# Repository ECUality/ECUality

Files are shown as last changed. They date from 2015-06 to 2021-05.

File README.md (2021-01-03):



# ECUality

This project is about taking full control of a dated fuel-injection system, and making that process easier to repeat. Currently, the system is built to run the engine in a 1984 VW vanagon. I aim to create a platform that bears adaptation requiring a minimum of external tools. 

ECUality differs from other ECU projects in that I avoid relying on complex tuning software, favoring simple map-tuning algorithms that run whenever the engine and O2 sensor are warm. 

More info [here](https://hackaday.io/project/4622-ecuality1).

## Install

1. Install the [Arduino IDE](https://www.arduino.cc/en/Main/Donate).
2. Clone the repository.
3. Connect an Arduino Mega 2560 to your computer's USB port.
4. Start the Arduino IDE.
5. Open `ECUality.ino` in the IDE.
6. Click "Upload". This will build the project, and upload the compiled firmware to your Arduino.

## License
[GNU GPLv3](LICENSE.txt)

## Dependencies
Platform: 8-bit Arduino Mega 2560 (The chip is AtMega 2560), atop the ECU shield specified in the shcematic and layout files.  
Build: Arduino IDE (uses gcc toolchain)

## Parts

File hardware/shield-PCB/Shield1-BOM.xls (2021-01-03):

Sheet: Part Locations
Item | location | nF | V | Package
2 | C1 | 10u | 35V | 1206
2 | C2 | 10u | 35V | 1206
2 | C3 | 10u | 35V | 1206
1 | C4 | 22u | 25V | 1206
8 | C5 | 100p | 50V | 1206 | First, select "Location" cell in item list
3 | C6 | 1u | 50V | 1206
2 | C7 | 10u | 35V | 1206
2 | C8 | 10u | 35V | 1206
4 | C9 | 220n | 50V | 1206
4 | C10 | 220n | 50V | 1206
4 | C11 | 220n | 50V | 1206
2 | C12 | 10u | 35V | 1206
6 | C13 | 4.7n | 50V | 1206
6 | C14 | 4.7n | 50V | 1206
5 | C15 | 100n | 50V | 1206
9 | C16 | 20p | 50V | 1206
4 | C17 | 220n | 50V | 1206
4 | C18 | 220n | 50V | 1206
7 | C19 | 1n | 50V | 1206
9 | C20 | 20p | 50V | 1206
2 | C21 | 10u | 35V | 1206
2 | C22 | 10u | 35V | 1206
8 | C23 | 100p | 50V | 1206
14 | R1 | 10k | 0.25W | 1206
15 | R2 | 4.7k | 0.25W | 1206
14 | R3 | 10k | 0.25W | 1206
18 | R4 | 10k | 0.25W | Trimmer
12 | R5 | 47k | 0.25W | 1206
19 | R6 | 0.04 | 5W | 27mm ax
16 | R7 | 18k | 600V | 1210
16 | R8 | 18k | 600V | 1210
16 | R9 | 18k | 600V | 1210
16 | R10 | 18k | 600V | 1210
16 | R11 | 18k | 600V | 1210
16 | R12 | 18k | 600V | 1210
16 | R13 | 18k | 600V | 1210
16 | R14 | 18k | 600V | 1210
15 | R15 | 4.7k | 0.25W | 1206
15 | R16 | 4.7k | 0.25W | 1206
13 | R17 | 22k | 0.25W | 1206
13 | R18 | 22k | 0.25W | 1206
15 | R19 | 4.7k | 0.25W | 1206
13 | R20 | 22k | 0.25W | 1206
11 | R21 | 220k | 0.25W | 1206
11 | R22 | 220k | 0.25W | 1206
11 | R23 | 220k | 0.25W | 1206
11 | R24 | 220k | 0.25W | 1206
10 | R25 | 1M | 0.25W | 1206
13 | R27 | 22k | 0.25W | 1206
13 | R28 | 22k | 0.25W | 1206
17 | R29 | 4.02k | 0.25W | 1206
17 | R30 | 4.02k | 0.25W | 1206
17 | R31 | 4.02k | 0.25W | 1206
17 | R32 | 4.02k | 0.25W | 1206
20 | D1 | Zener | 20V | SOD123
21 | D2 | Zener | 4.7V | SOD123
 | D7 | Zener | 4.7V | SOD123
22 | IC1 | buffer |  | SOT23-5
22 | IC2 | buffer |  | SOT23-5
22 | IC3 | buffer |  | SOT23-5
23 | IC4 | Vreg | 3.3V | SOT223
22 | IC5 | buffer |  | SOT23-5
29 | IC6 | Ign./Inj. IC |  | SO32W
43 | IC7 | comparator | 5V | SOT23-5
24 | IC8 | Vreg | 5V 1% | SOT223
24 | IC9 | Vreg | 5V 1% | SOT223
35 | IC11 | knock_IC |  | SO20L
26 | Q1 | IGBT | 390V | D2PAK
26 | Q2 | IGBT | 390V | D2PAK
26 | Q3 | IGBT | 390V | D2PAK
26 | Q4 | IGBT | 390V | D2PAK
27 | Q5 | P-MOS | 40V | D-PAK
28 | U$1 | Conn. | VW | 25-pin
30 | U$3 | SD holder
31 | U$4 | WBO2 controller
32 | Q6 | N-MOS | 3.3A | SOT23-3
33 | Q7 | N-MOS | 300mA | SOT23-3
34 | Q8 | Hi-side |  | D-PAK5
36 | QF1 | Crystal | 16MHz | HC49U
37 | ARD | Mega2560
38 | XB1 | X-bee 1
39 | FUSE1 | PTC fuse | .1A | 1206
40 | H1 | pin-header | 1x8 | .1"
40 | H2 | pin-header | 1x8 | .1"
40 | H3 | pin-header | 1x8 | .1"
40 | H4 | pin-header | 1x8 | .1"
41 | H5 | pin-header | 2x8 | .1"
42 | H6 | fem-header | 1x10 | 2mm
42 | H7 | fem-header | 1x10 | 2mm
44 | H8 | fem-header | 2x5 | .1"
45 | H9 | pin-header | 2x5 | .1"

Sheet: Unique Items
Item | location | nF | V | Package | Qty | pkg. type | Dist. PN
1 | C4 | 22u | 25V | 1206 | 1 | smt | 1276-3299-1-ND
2 | C1 C2 C3 C7 C8 C12 C21 C22 | 10u | 35V | 1206 | 8 | smt | 1276-3100-1-ND
3 | C6 | 1u | 50V | 1206 | 1 | smt | 1276-1068-1-ND
4 | C9 C10 C11 C17 C18 | 220n | 50V | 1206 | 5 | smt | 1276-1106-1-ND
5 | C15 | 100n | 50V | 1206 | 1 | smt | 1276-1017-1-ND
6 | C13 C14 | 4.7n | 50V | 1206 | 2 | smt | 1276-1309-1-ND
7 | C19 | 1n | 50V | 1206 | 1 | smt | 1276-1050-1-ND
8 | C5 C23 | 100p | 50V | 1206 | 2 | smt | 1276-1053-1-ND
9 | C16 C20 | 20p | 50V | 1206 | 2 | smt | 1276-2819-1-ND
10 | R25 | 1M | 0.25W | 1206 | 1 | smt | 311-1.00MFRCT-ND
11 | R21 R22 R23 R24 | 220k | 0.25W | 1206 | 4 | smt | 311-220KFRCT-ND
12 | R5 | 47k | 0.25W | 1206 | 1 | smt | 311-47.0KFRCT-ND
13 | R17 R18 R20 R27 R28 | 22k | 0.25W | 1206 | 5 | smt | 311-22KERCT-ND
14 | R1 R3 | 10k | 0.25W | 1206 | 2 | smt | 311-10.0KFRCT-ND
15 | R2 R15 R16 R19 | 4.7k | 0.25W | 1206 | 4 | smt | 311-4.70KFRCT-ND
16 | R7 R8 R9 R10 R11 R12 R13 R14 | 18k | 600V | 1210 | 8 | smt | RHM18KAICT-ND
17 | R29 R30 R31 R32 | 4.02k | 0.25W | 1206 | 4 | smt | RHM4.02KAICT-ND | 29
18 | R4 | 10k | 0.25W | Trimmer | 1 | smt | ST4ETA103CT-ND
19 | R6 | 0.04 | 5W | 27mm ax | 1 | thru-hole | 15FR040E-ND
20 | D1 | Zener | 20V | SOD123 | 1 | smt | 568-6359-1-ND
21 | D2 | Zener | 4.7V | SOD123 | 1 | smt | 568-6369-1-ND
22 | IC1 IC2 IC3 IC5 | buffer |  | SOT23-5 | 4 | smt | 296-11603-1-ND
23 | IC4 | Vreg | 3.3V | SOT223 | 1 | smt | AP1117IE33G-13DICT-ND
24 | IC8 IC9 | Vreg | 5V 1% | SOT223 | 2 | smt | AP1117E50GDICT-ND |  | MC33269ST-3.3T3GOSCT-ND
25 |  | op-amp | 5V | SOT23-5 | 0 | smt | MCP601T-E/OTCT-ND
26 | Q1 Q2 Q3 Q4 | IGBT | 390V | D2PAK | 4 | smt | ISL9V5036S3STCT-ND
27 | Q5 | P-MOS | 40V | D-PAK | 1 | smt | SUD50P04-09L-E3CT-ND
28 | U$1 | Conn. | VW | 25-pin | 1 | thru-hole | Re-used from VW original
29 | IC6 | Ign./Inj. IC |  | SO32W | 1 | smt | MCZ33810EK-ND
30 | U$3 | SD holder |  |  | 1 | thru-hole | HR1941CT-ND |  | top right pad needs to move right, two bottom pads need to have solder-stop masked (they
31 | U$4 | WBO2 controller |  |  | 1 | smt | Empty |  | re covered
32 | Q6 | N-MOS | 3.3A | SOT23-3 | 1 | smt | SI2304DDS-T1-GE3CT-ND
33 | Q7 | N-MOS | 300mA | SOT23-3 | 1 | smt | 568-1369-1-ND
34 | Q8 | Hi-side |  | D-PAK5 | 1 | smt | BTS6133DCT-ND
35 | IC11 | knock_IC |  | SO20L | 1 | thru-hole | 296-34575-5-ND
36 | QF1 | Crystal | 16MHz | HC49U | 1 | NA | XC1925-ND
37 | ARD | Mega2560 |  |  | 1 | thru-hole | 1050-1018-ND
38 | XB1 | X-bee 1 |  |  | 1 | smt | XB24-AWI-001-ND
39 | FUSE1 | PTC fuse | .1A | 1206 | 1 | smt | 507-1477-1-ND
40 | H1 H2 H3 H4 | pin-header | 1x8 | .1" | 4 | smt | 732-5371-ND
41 | H5 | pin-header | 2x8 | .1" | 1 | smt | 732-5466-5-ND
42 | H6 H7 | fem-header | 1x10 | 2mm | 2 | thru-hole | S5751-10-ND
43 | IC7 | comparator | 5V | SOT23-5 | 1 | smt | MCP6561UT-E/OTCT-ND
44 | H8 | fem-header | 2x5 | .1" | 1 | smt | S5714-ND
45 | H9 | pin-header | 2x5 | .1" | 1 | thru-hole | 609-3372-ND
 | notes:

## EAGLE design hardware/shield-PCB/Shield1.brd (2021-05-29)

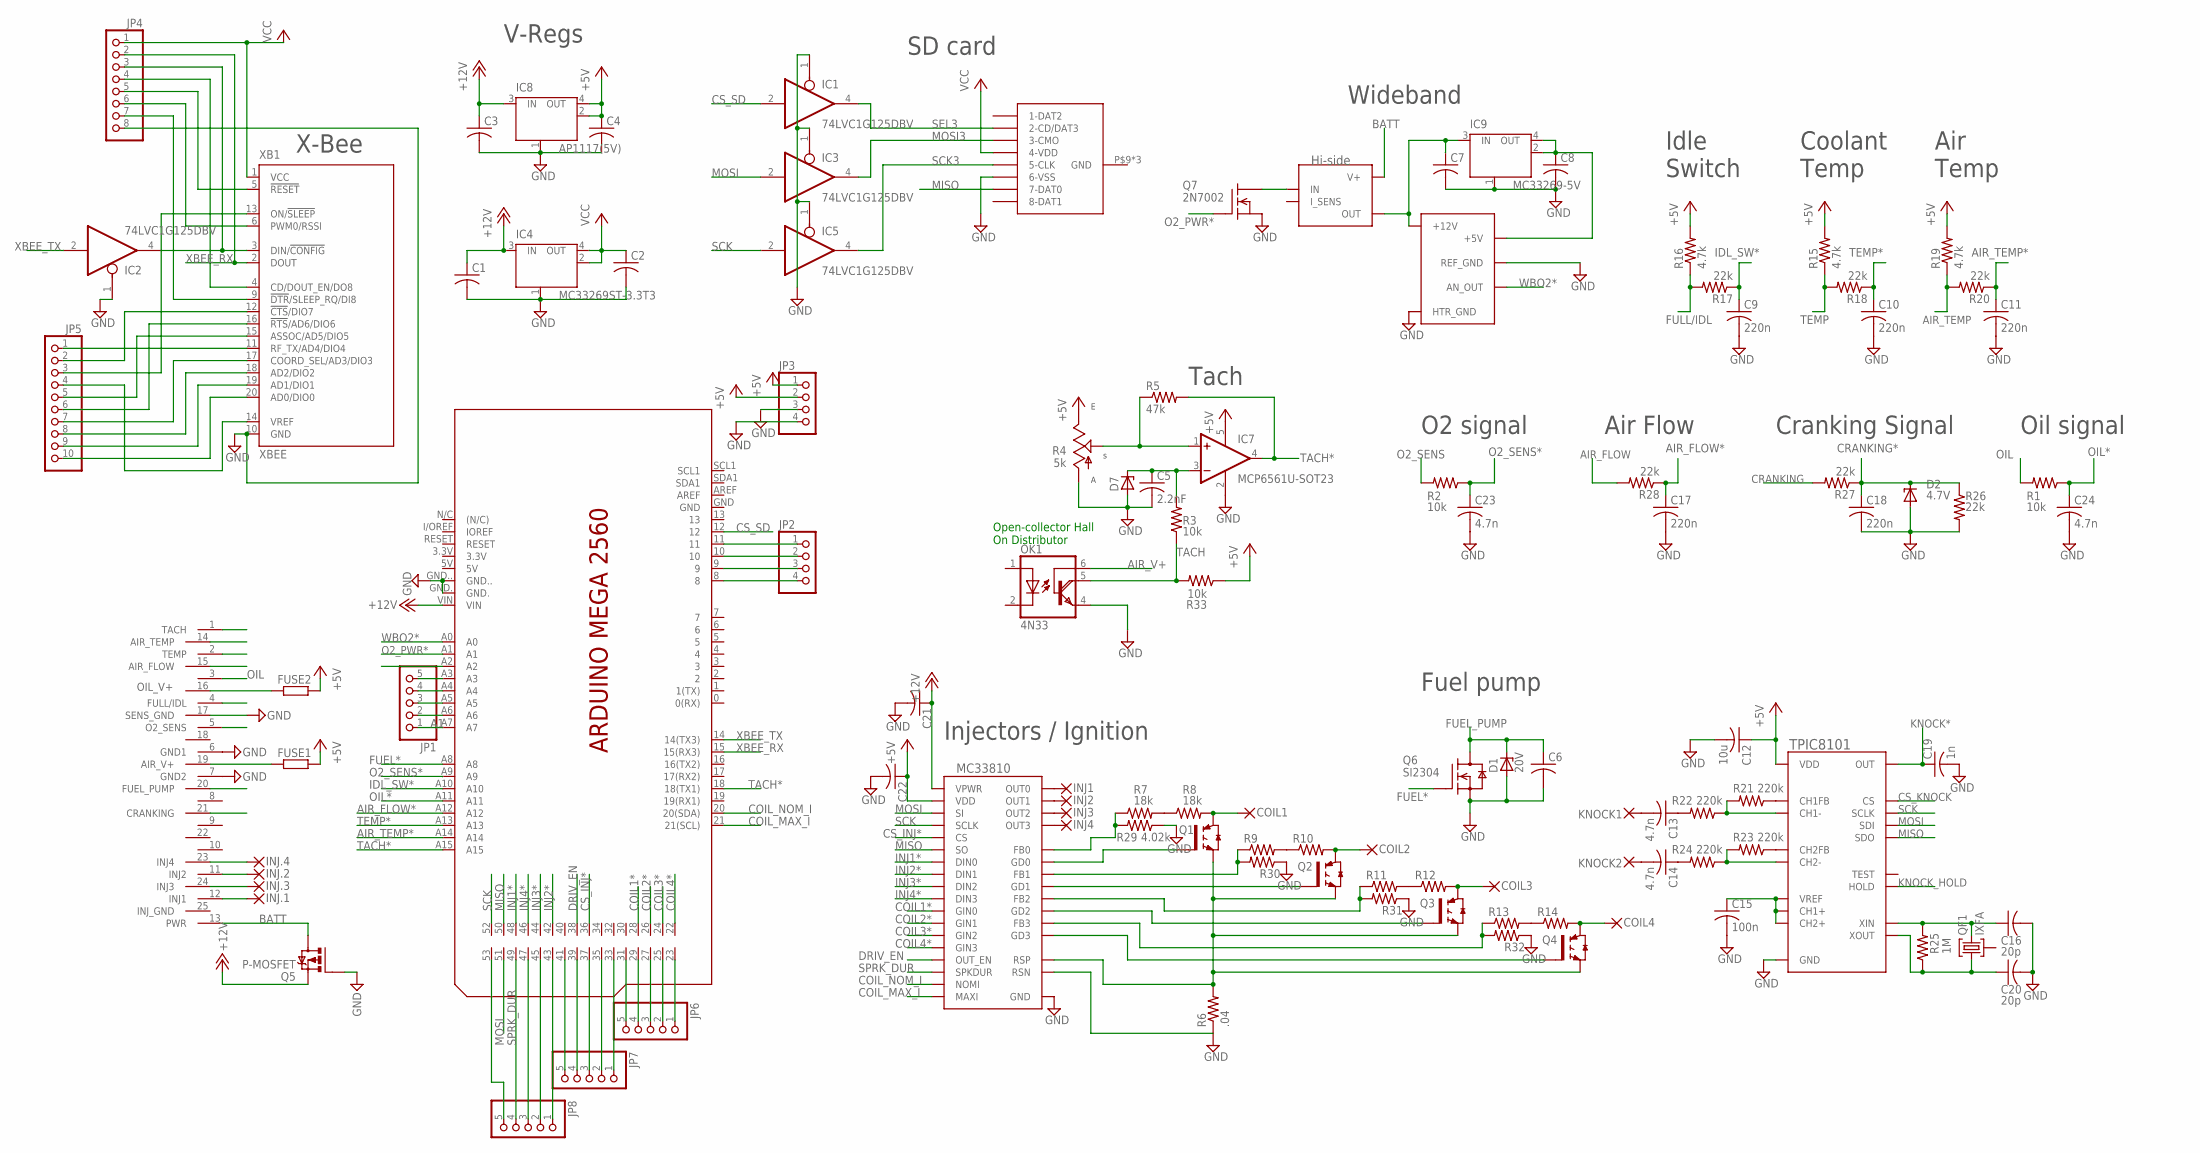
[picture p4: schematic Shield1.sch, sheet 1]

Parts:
C1, C2, C3, C4, C6, C7, C8, C21, C22: C-USC1206; C1206
C5: 2.2nF; C1206
C9, C10, C11, C17, C18: 220n; C1206
C12: 10u; C1206
C13, C14, C23, C24: 4.7n; C1206
C15: 100n; C1206
C16, C20: 20p; C1206
C19: 1n; C1206
COIL1, COIL2, COIL3, COIL4: 2,15/1,0
D1: 20V; SOD123
D2: 4.7V; SOD123
D7: ZENER-DIODESOD80C; SOD80C
FUSE1, FUSE2: R-EU_R1206W; R1206W
IC1, IC2, IC3, IC5: 74LVC1G125DBV; SOT23-5
IC4: MC33269ST-3.3T3; SOT223
IC6: MC33810SSOP; SSOP32_POWERPAD
IC7: MCP6561U-SOT23; SOT23-5
IC8: AP1117(5V); SOT223
IC9: MC33269-5V; SOT223
IC11: KNOCK_SENS_IC_TPIC8101; SO20L
INJ1, INJ2, INJ3, INJ4, INJ.1, INJ.2, INJ.3, INJ.4: 2,15/1,2
JP1, JP6, JP7, JP8: PINHD-1X5; 1X05
JP2, JP3: PINHD-1X4; 1X04
JP4: PINHD-1X8; 1X08
JP5: PINHD-1X10NARROW; 1X10-N
KNOCK1, KNOCK2: 2,15/1,0
OK1: 4N33; DIL06
Q1, Q2, Q3, Q4: ISL9V5036S3S; D2PACK
Q5: P-MOSFET; D-PAK_TO252AA
Q6: SI2304; SOT23
Q7: 2N7002; SOT23
Q8: BTS6133; DPACK_5
QF1: IXFA; HC49U
R1, R2, R3, R33: 10k; R1206
R4: 5k; 50/45J
R5: 47k; R1206
R6: .04; 0840/27
R7, R8: 18k; R1210W
R9, R10, R11, R12, R13, R14: R-US_R1210W; R1210W
R15, R16, R19: 4.7k; R1206
R17, R18, R20, R26, R27, R28: 22k; R1206
R21, R22, R23, R24: 220k; R1206
R25: 1M; R1206
R29: 4.02k; R1206
R30, R31, R32: R-US_R1206; R1206
U$1: VW_84_CONN
U$3: HI-ROSE-DM3D; DM3D-SF
U$4: ECOTRON_ALM-BOARD; ECOTRONS_ALM-BOARD
U$9: MEGA2560_SMD; MEGA_NO-PWR/USB/ICSP_SMD
XB1: XBEE

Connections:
+5V: C4.1, C12.1, C22.1, FUSE1.2, FUSE2.2, IC6.8 (VDD), IC7.5 (V+), IC8.2 (OUT), IC8.4 (OUT), IC11.1 (VDD), JP3.1, JP3.2, R4.1 (E), R15.2, R16.2, R19.2, R33.1
+12V: C1.1, C3.1, C21.1, IC4.3 (IN), IC6.25 (VPWR), IC8.3 (IN), Q5.3 (S), U$9.VIN
A1: JP1.1, U$9.A7
AIR_FLOW: R28.2, U$1.15 (AIR_FLOW)
AIR_FLOW*: C17.1, R28.1, U$9.A12
AIR_TEMP: R19.1, R20.2, U$1.14 (AIR_TEMP)
AIR_TEMP*: C11.1, R20.1, U$9.A14
AIR_V+: FUSE1.1, OK1.6 (B), U$1.19 (AIR_V+)
BATT: Q5.4 (D), Q8.3 (V+), U$1.13 (PWR)
COIL1: COIL1.1, Q1.2 (C), R8.2
COIL1*: IC6.24 (GIN0), U$9.28
COIL2: COIL2.1, Q2.2 (C), R10.2
COIL2*: IC6.23 (GIN1), U$9.26
COIL3: COIL3.1, Q3.2 (C), R12.2
COIL3*: IC6.22 (GIN2), U$9.24
COIL4: COIL4.1, Q4.2 (C), R14.2
COIL4*: IC6.21 (GIN3), U$9.22
COIL_MAX_I: IC6.29 (MAXI), U$9.21 (21(SCL))
COIL_NOM_I: IC6.28 (NOMI), U$9.20 (20(SDA))
CRANKING: R27.2, U$1.21 (CRANKING)
CRANKING*: C18.1, D2.C, R26.1, R27.1
CS_INJ*: IC6.4 (CS), U$9.36
CS_KNOCK: IC11.8 (CS)
CS_SD: IC1.2 (I), U$9.12
DRIV_EN: IC6.9 (OUT_EN), U$9.38
FUEL*: Q6.1 (G), U$9.A8
FUEL_PUMP: C6.1, D1.C, Q6.3 (D), U$1.20 (FUEL_PUMP)
FULL/IDL: R16.1, R17.2, U$1.4 (FULL/IDL)
GND: C1.2, C2.2, C3.2, C4.2, C5.2, C6.2, C7.2, C8.2, C9.2, C10.2, C11.2, C12.2, C15.2, C16.2, C17.2, C18.2, C19.2, C20.2, C21.2, C22.2, C23.2, C24.2, D1.A, D2.A, D7.A, IC1.1 (OE), IC1.3 (GND), IC2.1 (OE), IC2.3 (GND), IC3.1 (OE), IC3.3 (GND), IC4.1 (GND/ADJ), IC5.1 (OE), IC5.3 (GND), IC6.27 (RSN), IC6.GND, IC6.V1 (GND), IC6.V2 (GND), IC6.V3 (GND), IC6.V4 (GND), IC6.V5 (GND), IC7.2 (V-), IC8.1 (GND/ADJ), IC9.1 (GND/ADJ), IC11.2 (GND), JP3.3, JP3.4, JP4.8, OK1.4 (E), Q5.1 (G), Q6.2 (S), Q7.2 (S), R4.3 (A), R6.1, R26.2, R29.1, R30.1, R31.1, R32.1, U$1.6 (GND1), U$1.7 (GND2), U$1.17 (SENS_GND), U$3.P$3 (6-VSS), U$3.P$9 (GND), U$3.P$10 (GND), U$3.P$11 (GND), U$4.P$2 (HTR_GND), U$4.P$3 (REF_GND), U$4.P$6 (REF_GND), U$4.P$9 (HTR_GND), U$9.GND., U$9.GND.., XB1.10 (GND)
IDL_SW*: C9.1, R17.1, U$9.A10
INJ1: INJ.1.1, U$1.12 (INJ1)
INJ1*: IC6.10 (DIN0), U$9.48
INJ2: INJ.2.1, U$1.11 (INJ2)
INJ2*: IC6.11 (DIN1), U$9.42
INJ3: INJ.3.1, U$1.24 (INJ3)
INJ3*: IC6.12 (DIN2), U$9.44
INJ4: INJ.4.1, U$1.23 (INJ4)
INJ4*: IC6.13 (DIN3), U$9.46
KNOCK*: C19.1, IC11.4 (OUT), U$9.A2
KNOCK_HOLD: IC11.7 (HOLD)
MISO: IC6.7 (SO), IC11.11 (SDO), U$3.P$2 (7-DAT0), U$9.50
MOSI: IC3.2 (I), IC6.6 (SI), IC11.12 (SDI), U$9.51
MOSI3: IC3.4 (O), U$3.P$6 (3-CMO)
unnamed: C5.1, D7.C, IC7.3 (-IN), R3.2
unnamed: C7.1, IC9.3 (IN), Q8.1 (OUT), Q8.5 (OUT), U$4.P$1 (+12V), U$4.P$10 (+12V)
unnamed: IC6.26 (RSP), Q1.3 (E), Q2.3 (E), Q3.3 (E), Q4.3 (E), R6.2
unnamed: IC6.14 (GD1), Q2.1 (G)
unnamed: IC6.2 (FB0), R7.1, R29.2
unnamed: IC6.3 (GD0), Q1.1 (G)
unnamed: Q7.3 (D), Q8.2 (IN)
unnamed: IC6.1 (OUT0), INJ1.1
unnamed: IC11.19 (CH1-), R21.2, R22.1
unnamed: IC7.1 (+IN), R4.2 (S), R5.1
unnamed: IC6.15 (FB1), R9.1, R30.2
unnamed: IC6.30 (GD2), Q3.1 (G)
unnamed: IC2.4 (O), JP4.3, XB1.3 (DIN/!CONFIG)
unnamed: C8.1, IC9.2 (OUT), IC9.4 (OUT), U$4.P$4 (+5V)
unnamed: IC6.31 (FB2), R11.1, R31.2
unnamed: IC6.19 (GD3), Q4.1 (G)
unnamed: IC11.18 (CH1FB), R21.1
unnamed: IC6.18 (FB3), R13.1, R32.2
unnamed: C13.1, R22.2
unnamed: IC11.16 (CH2-), R23.2, R24.1
unnamed: C14.1, R24.2
unnamed: C15.1, IC11.3 (VREF), IC11.15 (CH2+), IC11.20 (CH1+)
unnamed: IC11.17 (CH2FB), R23.1
unnamed: IC6.16 (OUT1), INJ2.1
unnamed: IC6.32 (OUT2), INJ3.1
unnamed: C20.1, IC11.10 (XOUT), QF1.1, R25.1
unnamed: C16.1, IC11.9 (XIN), QF1.3, R25.2
unnamed: IC6.17 (OUT3), INJ4.1
unnamed: C13.2, KNOCK1.1
unnamed: C14.2, KNOCK2.1
unnamed: JP6.1, U$9.23
unnamed: R7.2, R8.1
unnamed: R9.2, R10.1
unnamed: R11.2, R12.1
unnamed: R13.2, R14.1
unnamed: JP1.2, U$9.A6
unnamed: JP1.3, U$9.A5
unnamed: JP1.4, U$9.A4
unnamed: JP1.5, U$9.A3
unnamed: JP2.1, U$9.11
unnamed: JP2.2, U$9.10
unnamed: JP2.3, U$9.9
unnamed: JP2.4, U$9.8
unnamed: JP4.4, XB1.4 (CD/DOUT_EN/DO8)
unnamed: JP4.5, XB1.5 (!RESET)
unnamed: JP4.6, XB1.6 (PWM0/RSSI)
unnamed: JP5.10, XB1.20 (AD0/DIO0)
unnamed: JP5.9, XB1.19 (AD1/DIO1)
unnamed: JP5.8, XB1.18 (AD2/DIO2)
unnamed: JP5.7, XB1.17 (COORD_SEL/AD3/DIO3)
unnamed: JP5.6, XB1.16 (!RTS!/AD6/DIO6)
unnamed: JP5.5, XB1.15 (ASSOC/AD5/DIO5)
unnamed: JP5.4, XB1.14 (VREF)
unnamed: JP5.3, XB1.13 (ON/!SLEEP)
unnamed: JP5.2, XB1.12 (!CTS!/DIO7)
unnamed: JP5.1, XB1.11 (RF_TX/AD4/DIO4)
unnamed: JP4.7, XB1.9 (!DTR!/SLEEP_RQ/DI8)
unnamed: JP6.2, U$9.25
unnamed: JP6.3, U$9.27
unnamed: JP6.4, U$9.29
unnamed: JP6.5, U$9.31
unnamed: JP7.1, U$9.33
unnamed: JP7.2, U$9.35
unnamed: JP7.3, U$9.37
unnamed: JP7.4, U$9.39
unnamed: JP7.5, U$9.41
unnamed: JP8.1, U$9.43
unnamed: JP8.2, U$9.45
unnamed: JP8.3, U$9.47
unnamed: JP8.5, U$9.53
O2_PWR*: Q7.1 (G), U$9.A1
O2_SENS: R2.2, U$1.5 (O2_SENS)
O2_SENS*: C23.1, R2.1, U$9.A9
OIL: R1.2, U$1.3
OIL*: C24.1, R1.1, U$9.A11
OIL_V+: FUSE2.1, U$1.16
SCK: IC5.2 (I), IC6.5 (SCLK), IC11.13 (SCLK), U$9.52
SCK3: IC5.4 (O), U$3.P$4 (5-CLK)
SEL3: IC1.4 (O), U$3.P$7 (2-CD/DAT3)
SPRK_DUR: IC6.20 (SPKDUR), JP8.4, U$9.49
TACH: OK1.5 (COL), R3.1, R33.2, U$1.1 (TACH)
TACH*: IC7.4 (OUT), R5.2, U$9.18 (18(TX1)), U$9.A15
TEMP: R15.1, R18.2, U$1.2 (TEMP)
TEMP*: C10.1, R18.1, U$9.A13
VCC: C2.1, IC1.5 (VCC), IC2.5 (VCC), IC3.5 (VCC), IC4.2 (OUT), IC4.4 (OUT), IC5.5 (VCC), JP4.1, U$3.P$5 (4-VDD), XB1.1 (VCC)
WBO2*: U$4.P$7 (AN_OUT), U$9.A0
XBEE_RX: JP4.2, U$9.15 (15(RX3)), XB1.2 (DOUT)
XBEE_TX: IC2.2 (I), U$9.14 (14(TX3))

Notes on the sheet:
Tach
Fuel pump
SD card
O2 signal
Injectors / Ignition
X-Bee
V-Regs
Wideband
Idle Switch
Air Temp
Coolant Temp
Air Flow
Cranking Signal
Oil signal
Open-collector Hall On Distributor

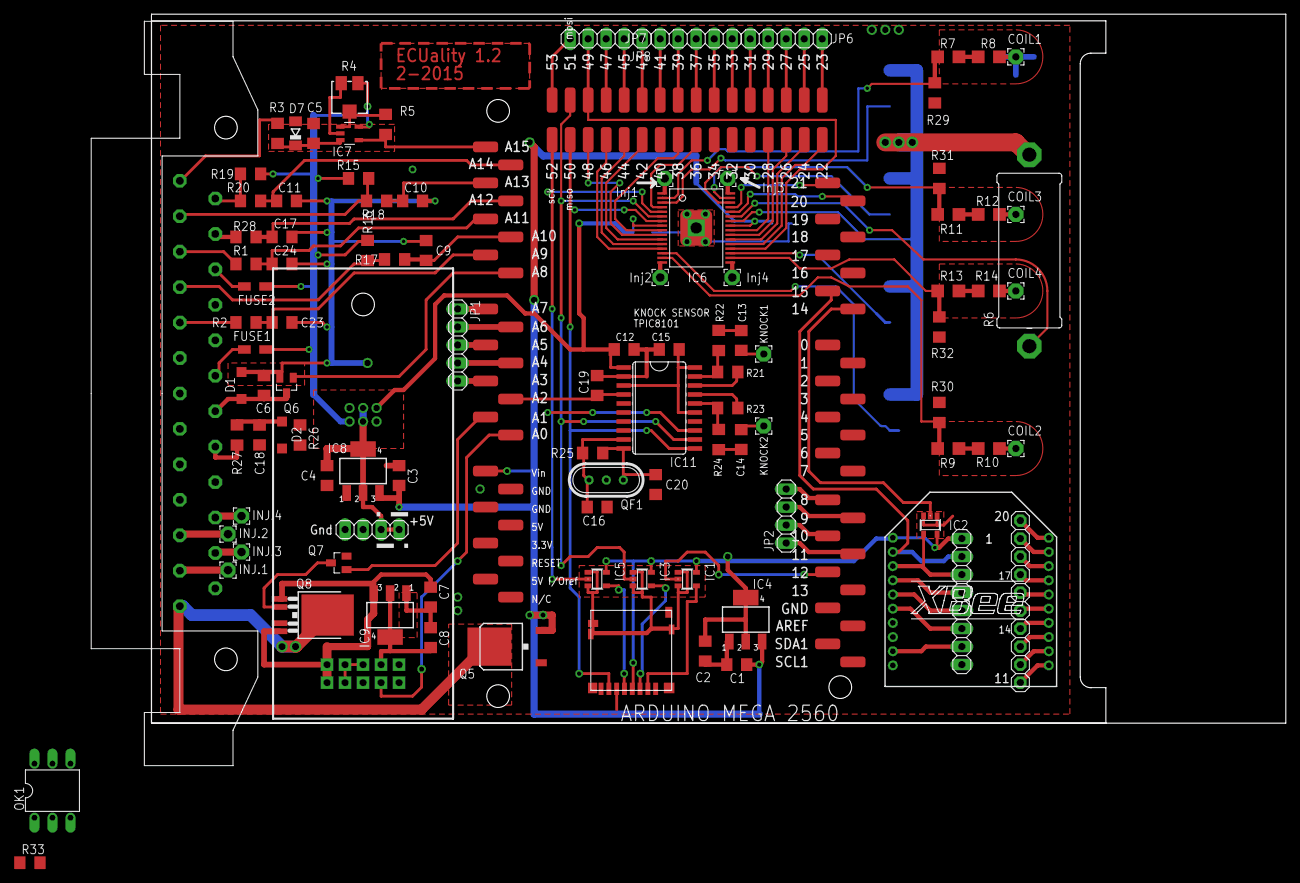
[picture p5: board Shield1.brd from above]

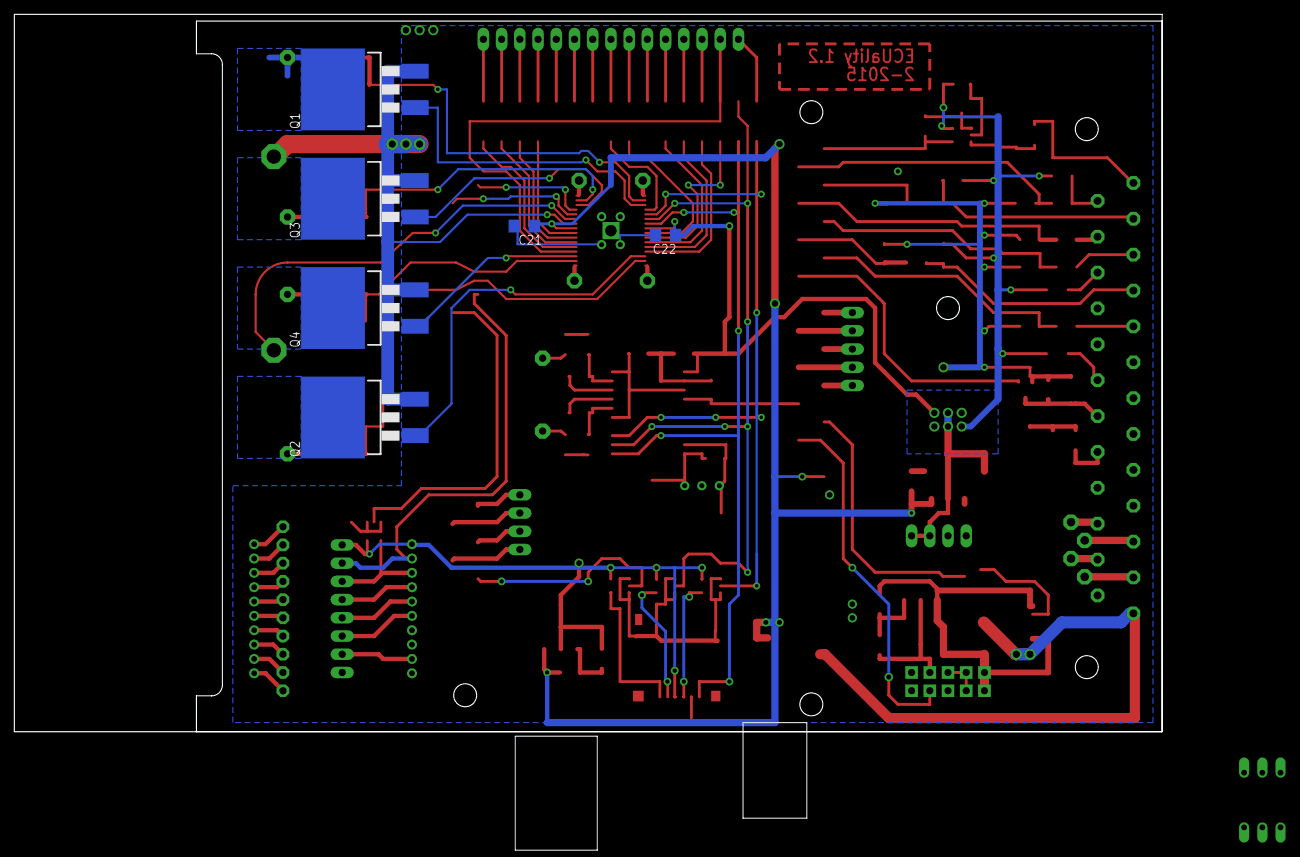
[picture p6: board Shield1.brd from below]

Board: 2 copper layers, 160.0 x 100.0 mm, 109 parts (7 on the bottom side), 129 nets.

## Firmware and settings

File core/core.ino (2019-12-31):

#include "Defines.h"
#include "Globals.h"
#include "Arrays.h"
#include "Map.h"
#include "Scale.h"
#include "Parameter.h"
#include "ECUSerial.h"
#include "ECUProtocol.h"
#include "Interpolation.h"
#include "EEIndex.h"
#include "EEPROMAnything.h"
#include "ECUPins.h"
#include "FuelTweaker.h"
#include "MovingAverage.h"
#include "SPICommands.h"
#include <EEPROM.h>
#include <SPI.h>

// Data: 60e6 us/min   16us/timer tic (256 prescale, 16Mhz)   
// quarter-rev of dizzy is measured 1/2 rev of crank
// us/min / us/tic  = tics/min
// tics / min * rev/sample = rev/min * tics/sample
// rev/min * tics/sample / tics/sample = rev/min 
// 60e6 / 16 / 2 = 1,875,000 rpm * tics/sample
// so rpm = 1875000/(spark_period)

#define TICS_PER_TACH 1875000

void addTask(void(*task)(), unsigned int ms);	// for some reason, this needs a prototype before it is used where others don't. 

void setup()
{
	char enable = 0;
	simulate_tach_en = 0;					// default to debug resources off. 
	fuel_pump_en = injector_en = coil_en = 1;	// default to having driving resources on. 

	ESerial.begin(9600);
	//Serial.begin(115200);

	InitSPI();

	NameParams();

	// There are 3 levels of priority in this program.  
	// Every event falls into one of these categories
	// 1: Injector duration timing (highest)
	// 2: Tasks that happen periodically (middle)
	// 3: Responses to the user (lowest)
	//
	// The following "task" array contains the periods of the level-2 events. 
	// Execution of these events can be interrupted by a level-1 event. 
	// These events will interrupt execution of a level-3 event. 
	n_tasks = 0;
	addTask(simulatedTachEdge, 20);
	addTask(readAirFlow, 50);
	addTask(readO2Sensor, 50);
	addTask(calcRPMandDwell, 50);
	addTask(calcInjDuration, 50);
	addTask(calcIgnitionMarks, 50);
	addTask(readAirTemp, 250);
	addTask(readCoolantTemp, 250);
	addTask(readOilPressure, 250);
	addTask(autoReport, 1000);
	addTask(updateRunCondition, 100);
	addTask(tweakFuel, TWEAK_FREQ_MS);

	i_autoreport = 8;		// this is referenced to delay next autoreport message.  

	// input interrupt pin
	digitalWrite(cs_knock_pin, HIGH);
	digitalWrite(cs_inj_pin, HIGH);
	digitalWrite(cs_sd_pin, HIGH);

	setPinModes(inputs, INPUT);
	setPinModes(outputs, OUTPUT);
	pinMode(40, INPUT);		// the other hooked-up inj1_pin. 
	pinMode(index_pin, INPUT_PULLUP);	// enable pullup on index pin. 

	digitalWrite(cs_inj_pin, HIGH);
	digitalWrite(cs_knock_pin, HIGH);
	digitalWrite(cs_sd_pin, HIGH);


	inj_duration = 5;
	tach_period = 0;

	Map::clear(&change_map);
	good_ee_loads = loadData(NULL);		// load data from EE.

	initProtocol();						// set up protocol. 

	// TIMERS
	// Configure Timer1 for task scheduling.  Hits ICR1 every 2ms and runs interrupt. 
	TCCR1A = 0;				// disables all output compare modules and clears WGM1<0-1> 
	TCCR1B = _BV(CS10);		// sets prescaler to 1:1, and turns on timer, clears WGM1<3:2>
	TCCR1B |= _BV(WGM12) | _BV(WGM13);	// 
	// WGM1<3:0> = 1,1,0,0 = mode 12 "CTC" with top = ICR.   positive slope only, 
	ICR1 = 32000;			// 16 tics / us * 2000us = 32000tics in 2ms.
	TIMSK1 = _BV(ICIE1);

	// Configure Timer3 for measuring injector pulse duration (using interrupt)
	TCCR3A = 0;							// clear control register A 
	TCCR3B = _BV(CS31) | _BV(CS30);		// start the timer at clk/64 prescale. 

	TIMSK3 |= _BV(OCIE3A);				// enable output compare A interrupt on timer 3
	//TIMSK3 |= _BV(TOIE3);				// enable timer overflow interrupt on timer 3 (just-in-case-of-something-weird)

	// Configure Timers 4 and 5 for measuring ignition dwell (using interrupt)
	TCCR4A = TCCR5A = 0;				// clear control register A 
	TCCR4B = _BV(CS42);					// start the timers at clk/256 prescale. = 16us per tic. 
	TCCR5B = _BV(CS52);
	//TCCR4B = _BV(CS42) | _BV(CS40);		// start the timer at clk/1024 prescale. = 64us per tic. 

	// enable timer overflow interrupt for non-running and slow-cranking issues
	TIMSK4 |= _BV(TOIE4);	// this affects rpm calculation for low RPM
	TIMSK5 |= _BV(TOIE5);


	// Timer4 NOTE: updateDwell() enables or disables the ignition system by 
	// setting or clearing OCIE4A, the output compare interrupt enable bit. 
	// The Output compare interrupt is what starts the dwells.
	// It is important for engine-start that we NOT set OCIE4A here. 


	// disable the timer 0 interrupt.  This breaks millis() but prevents interference with pulse timing.
	// note: ECUSerial.cpp uses millis() to time communication-stream events.  
	//TIMSK0 &= 0x00;		

	// Configure Timer0 for generating a fast PWM.  16us period, 62.5kHz
	// CONFIG BITS:
	// WGM0<3:0>	= 0 (0000)	normal mode, counts up to 0xFFFF.  
	// COM0A<1:0>	= 2 (10)	clears OC0A on compare match so OCR0A represents "high" time. 
	// COM0B<1:0>	= 2 (10)	same as A.
	// CS0<2:0>		= 1 (001)	1:1 pre-scaling, timer running. 

	// next line: the input circuit inverts the signal, so a rising edge from the distributor produces a falling
	// edge at the Arduino.  We trigger when the tab enters the Hall sensor.  The hall sensor produces a high signal
	// when it is looking at a tab, so we want to trigger here on a FALLING edge. 

	attachInterrupt(tach_interrupt, isrTachEdge, FALLING);	// interrupt 4 maps to pin 19. 	
	attachInterrupt(coil_current_interrupt, isrCoilNominalCurrent, RISING);	// interrupt 3 maps to pin 20. 

	EEPROM_readAnything(ENABLE_ADDY, enable);
	if (enable)
		enableDrive();
	else
		ESerial.println(F("engine disabled"));		// said to either my forgetful self, or a van-thief. 

	EEPROM_readAnything(TWEAK_LOCK_ADDY, boss.lockout);
	if (boss.lockout)
		ESerial.println(F("tweaks locked"));		// lock bit set, no tuning. 

	auto_stat = 1; // turn on auto-reporting. 

	// following sets an 8ms timeout on dwell with soft shutdown. 
	// it must come some significant time after SPIInit().  Hence this placement. 
	SPIInitSparkMode();	
	_delay_us(1000);
	SPISetNOMI(nom_coil_current.value);
}

void addTask(void(*task)(), unsigned int ms)
{
	task_list[n_tasks] = task;
	ms_freq_of_task[n_tasks] = ms;
	n_tasks++;
}

void setPinModes(const uint8_t pins[], const uint8_t direction)
{
	char i = 0;
	while (1)
	{
		if (pins[i] == '\0')
			return;
		pinMode(pins[i], direction);
		++i;
	}
}

void loop()
{
	// reportStatus is queued for action in the task scheduler but called here because serial output
	// takes forever and doesn't have as high a priority as running the engine. 
	if (auto_stat == 2)
	{
		auto_stat = 1;
		reportStatus(status_mode);
	}

	// check for any available serial input, then parse and run the commands. 
	ESerial.executeCommand();	
}

void autoReport()
{
	if (auto_stat == 1)
		auto_stat = 2;
	return;
}

// Sensor reading functions
void readAirFlow()
{

	air_flow_d = -air_flow;
	air_flow = analogRead(air_flow_pin) >> 2;	// takes 100us.  Should shorten
	air_flow_d += air_flow;

	if (air_flow_d > 20)
	{
		n_air_faults++;
		//ESerial.print(F("!air flt: "));
		//ESerial.println(n_air_faults);
	}

	/*
	air_flow_snap += air_flow_d;

	if (air_flow_snap)
	{
		if (air_flow_snap > accel_stabilize_rate.value)
			air_flow_snap -= accel_stabilize_rate.value;
		else
			air_flow_snap = 0;
	} */
	

}
void readO2Sensor()
{
	//o2_d = -o2;
	o2 = analogRead(o2_pin);		// this takes 100us.  Should shorten
	o2 *= 5; 
	//o2_d += o2;
}
void readAirTemp() 
{
	air_temp = analogRead(air_temp_pin);
	air_temp = temp_scale.interpolate(air_temp);
}
void readCoolantTemp() 
{
	coolant_temp = analogRead(coolant_temp_pin);
	coolant_temp = temp_scale.interpolate(coolant_temp);
}
void readOilPressure()
{
	// .5V = 0psi  4.5V = 100psi.  25psi/V 
	// 25psi/V * 5V/1023tic = .1222 psi/tic
	// 1 psi ~ 8 tics. 
	oil_pressure = analogRead(oil_pressure_pin);
}
void calcRPMandDwell()
{
	static uint16_t old_rpm = 0;
	static uint16_t l_tach_period; // a local to this function copy of the volatile tach-period
	char cSREG;

	cSREG = SREG; // store SREG value - we don't assume GIE is set, we just copy it. 
	cli(); //disable interrupts during copy
	l_tach_period = tach_period;
	SREG = cSREG; /* restore SREG value (GIE-bit) to what it was*/

	// (60e6 us/min) / (4 us/tic)				= 15e6 tics/min
	// (tics/min) / (tach_period tics/pulse)	= pulses/min
	// pulses/min * (1 rev/pulse)				= 15e6 / tach_period 
	// we're pulsing the injectors (and measuring) every other tach input pulse, so it's 1:1 with crankshaft. 
	old_rpm = rpm;

	rpm = TICS_PER_TACH / l_tach_period;		// tach_period_copy doesn't get touched by interrupts, so this is safe. 
	rpm_d = old_rpm - rpm;
	avg_rpm.addSample(rpm);
	
	// This section says if we're running, and the rpm makes an abrupt change, 
	// it's a fault.  Log it.  
	if (!(run_condition & _BV(NOT_RUNNING) ) && (abs(rpm_d) > 1000))
	{
		if (rpm > avg_rpm.average)
		{
			n_rpm_hi_faults++;
			//ESerial.print("!RPM xtra ");
			//ESerial.println(n_rpm_hi_faults);
		}
		else
		{
			n_rpm_lo_faults++;
			//ESerial.print(F("!RPM miss "));
			//ESerial.println(n_rpm_lo_faults);
		}
	}
	
	// Only start charging coil if RPM is above a minimum and the rpm is relatively stable
	if ((rpm > MIN_IGN_RPM) && (abs(rpm_d) < (rpm >> 2)))
	{
		// clear the output compare flag. 
		TIFR4 &= ~(_BV(OCF4A) | _BV(OCF4B));	// clear the output compare flags. 
		TIFR5 &= ~(_BV(OCF5A) | _BV(OCF5B));	

		TIMSK4 |= (_BV(OCIE4A) | _BV(OCIE4B));	// enable the out.comp. interrupt (ignition system)
		TIMSK5 |= (_BV(OCIE5A) | _BV(OCIE5B));	

		digitalWrite(drv_en_pin, LOW);		// enable the driver chip (active low)
	}
	else
	{
		// disable ignition system. 
		TIMSK4 &= ~_BV(OCIE4A);			// this prevents the coil pin from being set
		TIMSK5 &= ~_BV(OCIE5A);	

		digitalWrite(drv_en_pin, HIGH);	// this starts a soft-shutdown - this pin active low
		PORTA &= 0xAA;			//  &= 1010_1010 turns off bits 0, 2, 4, and 6 (turns off all coils). 
	}

	// Use a fixed dwell for cranking.  Otherwise adjust the dwell to match a target current. 
	if (rpm < 800 && digitalRead(cranking_pin) ) {
		g_dwell = starting_dwell.value;		// High dwell during cranking
	}
	else {
		if (coil_current_flag) g_dwell--;
		else g_dwell++;
	}

}

// Pulse duration business
void calcInjDuration()
{
	static unsigned int l_inj_duration;
	static int accel_offset, choke_offset, air_temp_offset, global_offset;

	if (digitalRead(cranking_pin))
	{
		map_inj_duration = cranking_dur.value;
		choke_offset = adjustForColdEngine(cranking_dur.value, coolant_temp);	
		l_inj_duration = map_inj_duration + choke_offset;
	}

	else if (run_condition & _BV(IDLING))	// only consider cold engine enrichment for idle.  No global correction. 
	{
		map_inj_duration = idle_offset.value + idle_scale.interpolate(rpm);
		choke_offset = adjustForColdEngine(map_inj_duration, coolant_temp);
		l_inj_duration = map_inj_duration + choke_offset;
	}

	else if (run_condition & _BV(COASTING))
	{
		map_inj_duration = 0;
		l_inj_duration = 0;
	}

	else
	{
		// find nominal
		map_inj_duration = inj_map.interpolate(rpm, air_flow, &offset_map);

		// adjust for stuff
		accel_offset = adjustForAccel(air_flow);		// these should not be order dependent.  
		choke_offset = adjustForColdEngine(map_inj_duration, coolant_temp);
		air_temp_offset = adjustForAirTemp(map_inj_duration, air_temp);
		global_offset = (map_inj_duration >> 8)*global_correction.value;

		l_inj_duration = map_inj_duration + accel_offset + choke_offset + air_temp_offset + global_offset;
	}

	// output that shit
	char cSREG;
	cSREG = SREG; // store SREG value - we don't assume GIE is set, we just copy it. 
	cli(); //disable interrupts during copy
	inj_duration = l_inj_duration;
	SREG = cSREG; /* restore SREG value (GIE-bit) to what it was*/
}

// Ignition advance business - executes immediately after calcInjDuration()
void calcIgnitionMarks() {
	static uint16_t dwell_mark, spark_mark;	// these are the timer settings for the dwell start and spark events.  
	static uint16_t l_tach_period;			// this is a local copy of the volatile tach_period.
	char cSREG;

	const uint16_t edge_to_post = 256;
	static uint16_t spark_position;

	// here we calculate the centrifugal advance (rpm based) 
	// the units are 1/512ths of a revolution to facilitate division speeds. 
	// the original timing  
	advance = rpm_advance.interpolate(rpm);
	/*if (rpm < 1100) advance = 0;
	else if (rpm < 2124) advance = (((rpm - 1100) * 5) >> 8);
	else if (rpm < 2380) advance = 20 + (((rpm - 2124) * 3) >> 7);
	else if (rpm < 4428) advance = 26 + (((rpm - 2380) * 5) >> 10);
	else advance = 35;*/

	// now we do the vacuum advance.  (light-load advance)
	// The engine load is indicated by the injector duration (how much fuel enters the cylinder every cycle) 
	// At sea-level, the maximum injector duration is about 1,800.  The minimum while coasting is about 500.  
	// Assuming 1800 = 1bar (absolute) and a linear scale, then 500 = .278 bar(abs) = .722 bar vacuum (21inHg)
	// The manual calls for vacuum advance to begin at .21 bar and max out at .36 bar, 14 degrees (= 20/512'ths)
	// Using the injector duration scale, .21 bar vacuum = .79 bar absolute = .79*1800 = 1422 inj.
	// Similarly, .36 bar vacuum = .64 bar absolute = 1152 injector.  
	advance += vacuum_advance.interpolate(map_inj_duration);

	/*if (map_inj_duration < 1200) advance += 20;
	else if (map_inj_duration < 1456) advance += (((1456 - map_inj_duration) * 5) >> 6);*/

	// That's it.  The advance can vary from 0 to 55.  1/512ths =  0 - 38.7 degrees. 
	// At 3500 rpm and inj_duration of 1200, we'll have 31(rpm) and 20(load) = 51/512 = 36 degrees. 


	//spark_position = edge_to_post + 28 - advance;	// advance varies from 0 to 55, so we center it with + 28. 
	spark_position = initial_retard.value - advance;

	cSREG = SREG; // store SREG value - we don't assume GIE is set, we just copy it. 
	cli(); //disable interrupts during copy to the volatile variables. 
	l_tach_period = tach_period; 
	SREG = cSREG; /* restore SREG value (GIE-bit) to what it was*/

	spark_mark = ( (unsigned long)spark_position * l_tach_period ) >> 8;	// mark = (bdeg of event) * (timer tics per 256 bdeg) / (256 bdeg). 

	dwell_mark = spark_mark > g_dwell ? spark_mark - g_dwell : 0;	// Make sure dwell_mark is never negative.  

	// disable interrupts while Output Compares are set. 
	cSREG = SREG; // store SREG value - we don't assume GIE is set, we just copy it. 
	cli(); //disable interrupts during copy to the volatile variables. 
	v_spark_mark = spark_mark;
	v_dwell_mark = dwell_mark;
	SREG = cSREG; /* restore SREG value (GIE-bit) to what it was*/

}
int adjustForAccel(int air_flow)
{
	return 0;
}
int adjustForColdEngine(unsigned int nominal_duration, int coolant_temp)
{
	// calculates a positive offset as a percentage of nominal injector duration. 
	// % increase depends linearly on coolant temperature.  
	// takes a threshold temp and a rate (mx +b) for linear dependence on  coolant temperature
	unsigned long adjustment;
	
	if (run_condition & _BV(WARM))		// is engine already warm? 
		return 0;

	adjustment = choke_scale.interpolate(coolant_temp);
	adjustment *= nominal_duration;
	adjustment >>= 10;		// divide by 1024
	return int(adjustment);	// adjustment;		XXX
}
int adjustForAirTemp(int nominal_duration, int air_temp)
{
	return 0;
}

void tweakFuel()
{
	boss.tweak();
}
void updateRunCondition()
{
	char idl_or_full = !digitalRead(idl_full_pin);
	run_condition = 0;

	if (digitalRead(cranking_pin))
		run_condition |= _BV(CRANKING);

	else if ((rpm < RUNNING_RPM) || !digitalRead(fuel_pin))
		run_condition |= _BV(NOT_RUNNING); 

	else if (idl_or_full && (air_flow < air_thresh.value))
		//(air_flow < coasting_air.interpolate(rpm))
	{
		if (rpm > coasting_rpm.value)
			run_condition |= _BV(COASTING);
		else
			run_condition |= _BV(IDLING);
	}

	else if (idl_or_full && (air_flow > air_thresh.value))
		run_condition |= _BV(WIDE_OPEN);

	if (coolant_temp >= cold_threshold.value)
		run_condition |= _BV(WARM);
}


// analog reading scaling
int scaleRead(int x, const int x_array[], const int y_array[], char n)
{
	char i;
	i = findIndexJustAbove(x_array, x, n);

	if (i > 0)	// reading is on the graph
		return linearInterp(x, x_array[i-1], x_array[i], y_array[i-1], y_array[i]);
	
	else if (i == 0)	// x is to left of graph.  Use leftmost points
		return linearInterp(x, x_array[0], x_array[1], y_array[0], y_array[1]);

	else				// x is to right of graph. Use rightmost points.
		return linearInterp(x, x_array[n-1], x_array[n], y_array[n-1], y_array[n]);
}

// important commands

// simple stuff
void toggle(unsigned char pin) 
{
	// Toggle LED
	digitalWrite(pin, digitalRead(pin) ^ 1);
}

/*********************** interrupt routines ***********************/
// Task scheduler interrupt 
ISR( TIMER1_CAPT_vect )			
{
	sei();

	// Some of these tasks take a while, and they all run within this interrupt's scope.
	// The timer might have enough time to reach the another input compare match, which 
	// would trigger another of these interrupts.  We have to keep global interrupts enabled
	// so the tach pulses CAN interrupt this interrupt, but if the task scheduler interrupts 
	// itself before finishing, we enter an endless loop and crash the stack.   
	// So we turn off the TIMER1 interrupts while we're in this ISR to prevent this. 
	TIMSK1 = 0;		
	static unsigned char i;
	static unsigned int task_start_time = 0; 
	
	for (i = 0; i < n_tasks; i++)
	{
		ms_since_last_task[i] += 2;				// tic eahc task's betwee-calls timer
		if (ms_since_last_task[i] >= ms_freq_of_task[i])	// is it time to call the task?
		{
			ms_since_last_task[i] = 0;			// reset this task's between-calls timer.

			task_start_time = TCNT1 >> 4;		// record start in us
			(*task_list[i])();						// call task i.
			task_runtime[i] = TCNT1 >> 4;		// record finish in us
			task_runtime[i] -= task_start_time;	// subtract to find runtime in us. 
		}
	}

	// We re-enable this interrupt now that we've gotten through the task list. 
	// as we do this, this interrupt may interrupt itself here, but 
	// all the tasks we were doing have had their "ms_since_last_task[i]"s cleared, 
	// so we'll blaze through the list and exit both nested ISRs. 
	TIMSK1 |= _BV(ICIE1);	
							
					
}

// Injectors open and spark events
void simulatedTachEdge() {
	// this function lets the ECU trigger its own tach based on the task scheduler timer (TIMER1)
	// useful for debugging electrical noise and such - the ECU can produce outputs without the engine running. 
	if (simulate_tach_en)
		isrTachEdge();
}
void isrTachEdge()
{
	static uint8_t next_active_coil = 0;

	if ( (PINA & _BV(PA7)) == 0 ) {	// check if index pin is low (triggered) digitalRead(index_pin) == LOW
		next_active_coil = 0x40;	// if index pin is low, set next active coil 
	}
	else {
		next_active_coil = next_active_coil >> 2;
	}

	// these fuel injection actions happen every other pulse.  We use pulse_divider to track which pulse we're on.
	static char pulse_divider = 0;	
	if (!pulse_divider)
	{
		// Ignition operations - we flip which counter we use based on the pulse_divider 
		tach_period = TCNT5;	// this was reset last edge, so this measures the most recent tab duration. 

		TCNT4 = 0;	// set a timer for when we begin dwell again
		OCR4A = v_dwell_mark;		// Set the Output compare value for dwell and sparking events.  
		OCR4B = v_spark_mark;
		timer4_coil = next_active_coil;

		// Fuel operations //
		GTCCR |= _BV(PSRSYNC);		// clear the prescaler. 
		TCNT3 = 0;					// start the timer over. 

		// set all injectors high (in same instruction)
		if (inj_duration && injector_en)
		{
			PORTL |= 0xAA;				// 0b 1010 1010;
			OCR3A = inj_duration; 
		}
		else
			OCR3A = 100;				// if inj_duration = 0, we keep OCR3A positive. 

		pulse_divider = 1;
	}
	else
	{
		// Ignition operations //
		tach_period = TCNT4;		// set last edge, so this measures only one tab 

		TCNT5 = 0;	// set a timer for when we begin dwell again
		OCR5A = v_dwell_mark;		// Set the Output compare value for dwell and sparking events.  
		OCR5B = v_spark_mark;
		timer5_coil = next_active_coil;
		--pulse_divider;
	}

}

// Injectors close event
ISR(TIMER3_COMPA_vect)			// this runs when TCNT3 == OCR3A. 
{
	// set all injectors low (in same instruction)
	PORTL &= ~0xAA;			// 0b01010101; 
}

// Begin dwell event
// Coil1: Arduino 28: Mega A6: 0b0100_0000, 0x40, 64
// Coil2: Arduino 26: Mega A4: 0b0001_0000, 0x10, 16
// Coil3: Arduino 24: Mega A2: 0b0000_0100, 0x04, 4
// Coil4: Arduino 22: Mega A0: 0b0000_0001, 0x01, 1

ISR(TIMER4_COMPA_vect)			// runs when TCNT4 == OCR4A. 
{
	StartDwell(timer4_coil);
}
ISR(TIMER5_COMPA_vect)			// same as for timer 4 but uses timer 5 so timer doesn't get reset before both compares happen
{
	StartDwell(timer5_coil);
}
void StartDwell(uint8_t active_coil)
{
	if (coil_en)
	{
		PORTA |= active_coil;		// coil is turned on; starts ign.coil dwell, in prep for spark
		//PORTA |= 0x08;			//(A3 is turned on for LED indication of function) 
		PORTA |= 0x08;				// turn on the LED
	}
}

// Spark event
ISR(TIMER4_COMPB_vect)
{
	Spark(timer4_coil);
}
ISR(TIMER5_COMPB_vect)
{
	Spark(timer5_coil);
}

void Spark(uint8_t active_coil)
{
	// check the NOMI pin.  If it's hi, set the coil_current_flag = 1.  Otherwise, = 0; 
	coil_current_flag = (PIND & _BV(PD1) != 0) ? 1 : 0;	// arduino pin 20 equates to Atmega port PD1 / SDA / INT1 
	PORTA &= ~active_coil;	// Opens coil circuit, causing spark. 
	//PORTA &= ~0x40;		// 0b 1011 1111 (A6 is turned off) Opens the ignition coil circuit, causing spark
	PORTA &= ~0x08;				//  turn off LED 
}

// De-energize ignition coil without spark (dwell exceeded maximum duration)
ISR(TIMER4_OVF_vect)
{
	tach_period = 65000;	// this makes it obvious the engine is not running 
							// rpm will be 1,875,000 / 65,000 = 28 rpm

	digitalWrite(drv_en_pin, HIGH);	// disables drive (active low).  This causes soft-shutdown of coil (no spark). 
}
ISR(TIMER5_OVF_vect)	// same as directly above. Different timer
{
	tach_period = 65000;	
	digitalWrite(drv_en_pin, HIGH);	// disables drive (active low).  This causes soft-shutdown of coil (no spark). 
}
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

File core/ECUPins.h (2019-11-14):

#pragma once

// Pin mappings /////////////////

// Input pins
const uint8_t air_flow_pin = A12;
const uint8_t air_temp_pin = A14;
const uint8_t o2_pin = A9;
const uint8_t coolant_temp_pin = A13;
const uint8_t oil_pressure_pin = A11;
const uint8_t tach_pin = 18;
const uint8_t index_pin = 29;	// PORTA-7
const uint8_t tach_interrupt = 5;		// see "attachinterrupt" page on Arduino.cc
const uint8_t coil_current_interrupt = 3;	// same as above www.arduino.cc
const uint8_t idl_full_pin = A10;
const uint8_t cranking_pin = 10;
const uint8_t coil_nom_i = 20;
const uint8_t coil_max_i = 21;

const uint8_t inputs[] = { air_flow_pin, air_temp_pin, o2_pin, coolant_temp_pin, oil_pressure_pin, tach_pin, index_pin,
idl_full_pin, cranking_pin, coil_nom_i, coil_max_i, '\0' };

// Output pins
const uint8_t inj2_pin = 42;
const uint8_t inj3_pin = 44;
const uint8_t inj4_pin = 46;
const uint8_t inj1_pin = 48;

const uint8_t coil1_pin = 28;
const uint8_t coil2_pin = 26;
const uint8_t coil3_pin = 24;
const uint8_t coil4_pin = 22;

const uint8_t fuel_pin = A8;
const uint8_t drv_en_pin = 38;
const uint8_t o2_pwr_pin = A1;
const uint8_t cs_knock_pin = 9;
const uint8_t cs_sd_pin = 12;
const uint8_t cs_inj_pin = 36;
const uint8_t inj_led_pin = 25;

uint8_t outputs[] = { inj1_pin, inj2_pin, inj3_pin, inj4_pin,
coil1_pin, coil2_pin, coil3_pin, coil4_pin,
fuel_pin, drv_en_pin, o2_pwr_pin,
cs_knock_pin, cs_sd_pin, cs_inj_pin, inj_led_pin, '\0' };

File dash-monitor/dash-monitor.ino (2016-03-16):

/*
LiquidCrystal Library - Serial Input

* LCD RS pin to digital pin 12
* LCD Enable pin to digital pin 11
* LCD D4 pin to digital pin 5
* LCD D5 pin to digital pin 4
* LCD D6 pin to digital pin 3
* LCD D7 pin to digital pin 2
* LCD R/W pin to ground
* 

Library originally added 18 Apr 2008
by David A. Mellis
library modified 5 Jul 2009
by Limor Fried (http://www.ladyada.net)
example added 9 Jul 2009
by Tom Igoe
modified 22 Nov 2010
by Tom Igoe

http://arduino.cc/en/Tutorial/LiquidCrystalSerial
*/

// include the library code:
#include <LiquidCrystal.h>
#include <IRLib.h>


// initialize Infrared receiver (measures pulses) and decoder (interprets pulses)
IRdecode My_Decoder;
IRrecv My_Receiver(42);	 // pin assigned

// initialize the library with the numbers of the interface pins
LiquidCrystal lcd(12, 11, 10, 9, 8, 7, 6);
HardwareSerial& ESerial = Serial1;
//LiquidCrystal& display = lcd; 

const unsigned long code[] = { 0xFFA25D, 0xFFE21D, 0xFF22DD, 0xFF02FD, 0xFFC23D, 0xFFE01F, 0xFFA857, 0xFF906F, 0xFF6897,
0xFF9867, 0xFFB04F, 0xFF30CF, 0xFF18E7, 0xFF7A85, 0xFF10EF, 0xFF38C7, 0xFF5AA5, 0xFF42BD, 0xFF4AB5, 0xFF52AD };

const char command[][6] = { "lock", "arm", "prep", "nxti", "nxtp", "save", "dbl", "hlf", "Sloc", "+", "-", 
	"auto1", "auto2", "auto3", "auto4", "auto5", "auto6", " ", " ", " " };

char text_line[16] = "";

#define IRpin_PIN PIND
#define IRpin 2

// for MEGA use these!
//#define IRpin_PIN PINE
//#define IRpin 4

void setup(){
	// set up the LCD's number of columns and rows: 
	lcd.begin(16, 2);
	// initialize the serial communications:
	ESerial.begin(9600);

	My_Receiver.enableIRIn();
}

void loop()
{
	char c; 
	uint8_t n_codes = (sizeof(code) / sizeof(code[0]));
	int i;

	// when characters arrive over the serial port...
	if (ESerial.available()) {
		// wait a bit for the entire message to arrive
		delay(100);

		// check if it's a fault (bottom row)
		if (ESerial.peek() == '!')
		{
			lcd.setCursor(0, 1);	// change to bottom row
			ESerial.read();				// eat the '!' character
		}

		else
			lcd.setCursor(0, 0);

		// read all the available characters
		for (int i = 0; i < 16; i++)
		{
			c = ESerial.peek();
			if (c < ' ')
				lcd.write(' ');
			else
				lcd.write(ESerial.read());

		}

		// dump the rest of the regular-character stream until we get special characters
		while (1)
		{
			c = ESerial.read();
			if (c < ' ')
				break;
		}
		// now dump the remaining characters (which will hopefully all be special)
		while (ESerial.available())
		{
			ESerial.read();
		}
			
	}

	if (My_Receiver.GetResults(&My_Decoder))
	{
		My_Decoder.decode();
		//My_Decoder.DumpResults();
		My_Receiver.resume();
		
		for (i = 0; i < n_codes; i++)
		{
			if (code[i] == My_Decoder.value)
			{
				ESerial.println(command[i]);
				break;
			} 
		}

	}
}

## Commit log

2015-03-16 Adding TimerOne-r11 library
2015-03-16 Nested interrupts working
2015-03-17 Switched to Atmel Studio
    Visual Studio Community 2013 started crashing repeatedly, starting with
    the first compile-upload to the mega 2560
2015-03-19 Switch back to VS13 community
    For memory and load speed reasons. This is verified to blink correctly
    using scheduler
2015-03-28 Pulse working, Interpolate written
    Pulse still has 7us interrupt conflict with other Arduino interrupts.
    Interpolate not tested.
2015-03-29 Map timings reproduced, TimerOne removed
    handled off-map cases and renamed some things
2015-03-30 Building post decomp attempt
    Learned: arduino has problems with "extern" and I should really try this
    with a simple program first.
2015-04-01 Pins mapped, outputs working
    injector driver is behaving, injector LED added. Also fixed bug where
    "coasting" just left the injectors open, and inverted full_idle input.
2015-04-02 Array-Scaling for Sensors and Choke
    Also added new choke scale to serial and eeprom for updating saving
    reporting and loading
2015-04-06 Added EEIndex, Scale classes
    Not tested yet, but building and communicating. Known issue with
    EEIndex having two initial zeros.
    [ECUSerial.h, Map.cpp, Scale.cpp]
2015-04-14 Added Tweaker, drove block
    Still has issue with local offsets drifting.
    [ECUSerial.cpp, FuelTweaker.cpp, Map.cpp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]
2015-04-14 Fixed signs in fuel tweaking mode 3
    Local and global tweaks road-tested drivable. Still need to fix stopped
    rpm detection.
    [FuelTweaker.cpp]
2015-04-21 Improve idle tuning (using RPM only now)
    Currently using the move-lean until rpm drops, then step back approach.
    This is used whether engine is warm or not. Very drive-able.
2015-05-07 Added support for wireless
    still has a bug with auto-reporting
    [ECUSerial.cpp, ECUSerial.h, FuelTweaker.cpp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]
2015-05-19 Wireless reporting oil
2016-03-16 IR remote can now adjust all Params/Scales
    Also added theft prevention
    [ECUProtocol.h, ECUSerial.cpp, FuelTweaker.cpp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]
2016-11-06 Cold engine idle bugfix
    Adds cold-engine enrichment while idling.
    [ECUSerial.cpp]
2016-11-07 Talking over SPI to MC33810
    Setting dwell timeout for ignition and added command to check status of
    both ignition and injection sides
2016-11-08 Driving ignition coil
    And measuring coil current, and handling start-up conditions.
2016-11-21 Change Tach input... Engine now starts
    The tach input was previously sourced from the the old ignition driver,
    which missed every 3rd or every other trigger event while the starter
    was cranking. This prevented the ECU from producing accurate dwell
    times while cranking. We now source timing directly from the hall
    effect (a wiring change in the harness), which produces the expected,
    consistent square wave. The signal is inverted, so we're back to rising
    edge trigger.
    [ECUProtocol.h]
2017-04-04 Speed up Dwell/RPM timer
    Switching to a new coil with lower primary resistance, I was charging
    this coil to high currents much faster. So the Dwell setting needed to
    be more accurate, so I dropped the prescale from 1/1024 to 1/256.
2017-04-05 New E-core coil / Tweak lockout persistent
    I-max for coil set to 16A / SetNomI() command added to help measure coil
    current on bench / Tweak-lock "lock" moved out of Tweaker class / Tweak
    lockout made persistent (EEPROM) / Dwell parameter limits changed /
    Parameter file updated.
2018-07-12 WIP: auto-tune upgrade/debug
    global correction now scales with nominal injector duration, every
    adjustment (tweak) affects both the global correction and local map (no
    more switching between local/global based on local_sum_limit logic).
    Distribution of correction to local map is now coarser but more
    deterministic (no integer division errors).
    [ECUProtocol.h, FuelTweaker.cpp, Map.cpp]
2018-07-12 Fixed type mismatch of rpm var in tweaker class
    The rpm variable is passed by reference to the boss object (FuelTweaker
    class). The FuelTweaker class was expecting a reference to a signed
    int, but it was given a reference to an unsigned int. So boss was
    always seeing an erroneous rpm value, which totally buggered where the
    changes to the local map were going.
    [ECUProtocol.h, FuelTweaker.cpp]
2018-07-12 Touching up parameter loading
    the "2" in the O2 parameter descriptions threw off the loading of data -
    TimedParseInt() saw the 2 as an int. So I replaced "O2" with "Oxy" and
    also nudged a few numbers.
    [FuelTweaker.cpp]
2018-07-30 Adhere to Arduino dumb naming convention.
2019-02-07 Adding Ign. timing Initial try
    Timing calculation working. Interrupts not working.
    [ECUProtocol.h, core.ino]
2019-02-07 Fixed overflow on multiplication bug
    timing is now looking good on scope.
    [Parameters 2-7-2019.txt]
2019-09-09 bugfix: overflow reg. update when cranking
    Injector duration calculation function was prematurely returning when the "Cranking" condition (as in, the starter motor is turning the engine) was true.
    [core.ino]
2019-09-10 Add simulated tach, on/off control of coil/inject
    These are tools to assist tracking down an electrical noise issue. With simulated Tach signal, I can run the various outputs of the ECU without the engine actually running. With on-off control of the output drivers, I can find the source of the noise by process of elimination.
    [ECUProtocol.h, ECUSerial.cpp, core.ino]
2019-09-10 Add prototype of new addTask() minor refactor
2019-09-11 Fixing bug with scheduled tasks
    Simulated Tach and control over coil, injectors and fuel pump now work
    [ECUProtocol.h, core.ino]
2019-11-14 Coil on plug coded but not starting
    Tested working with the lathe spinning the distributor, but on van,
    does not work. Appears the timing is not consistent. Van will catch
    a stroke or two, and subsequently stop, and with continued cranking,
    occasionally kick back as though spark is too advanced.
    [ECUPins.h, core.ino]
2019-11-15 Replace digitalRead() for cyl index check
    Now using PINA for direct port manipulation. Added various comments.
    [core.ino]
2019-11-18 Indexed Cylinder timing fixed
    Previously, the cylinder Cylinder 1 selection was handled in Tach-edge
    interrupt, and cylinder switching 1-to-2-to-3-to-4 was handled on
    dwell interrupt (TMR4/5). Sometimes the dwell interrupt happened
    just before the tach-edge, sometimes just after. This would mess up
    timing. To solve, I moved all cylinder select logic to tach-edge isr.
    [core.ino]
2019-12-31 Dwell now auto-adjusted to NOMI
    Auto-7 output now prints dwell. NOMI pin is measured on spark,
    if it's high, then g_dwell gets decremented. If it's low,
    g_dwell gets incremented. nom_coil_current is now a parameter.
    with range 0-31 where 0 = 3.0A and each tic is .25A more.
2021-01-03 Add shield design and reference
    [Shield1-BOM.xls, Shield1.brd, Shield1.sch]
2021-05-29 Update schematic to show tach power and pullup
    [Shield1.brd, Shield1.sch]
